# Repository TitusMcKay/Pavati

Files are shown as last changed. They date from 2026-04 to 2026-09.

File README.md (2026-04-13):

so here is some text in the md file idk how to ***write*** md but i should eventualy lol

i learned how to ssh keygen and use that for auth and can now push this new line over ssh
# About
In this repo are files for the battery signal delay box for the Pavati boats
The pcb designs were done in KiCad
The 3d models will be done in FreeCAD

# How To Source Components
To select components for procurment see [procurment.md](./procurment.md)

There is a [bom](https://en.wikipedia.org/wiki/Bill_of_materials) in [battery switch delay.tsv](./battery%20switch%20delay.tsv) that can be used to place manufatuer part numbers on the procurment list 

# How to view
## PCB
To view in the web go [here](https://kicanvas.org/?repo=https%3A%2F%2Fgithub.com%2FTitusMcKay%2FPavati)

To view on your machine clone the repo and open the project in KiCad

## 3D
You can view the case [here](https://3dviewer.net/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).

If you want the best viewing experience open the [design files](./3d) in [FreeCAD](https://github.com/freecad/freecad), or open .step files in your 3d printer slicer or CAD software of choice

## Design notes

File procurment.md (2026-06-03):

# Instructions
Use this list to add parts to an order from a market place like DigiKey or Mouser.

# Electronic Components

## Capacitors

C1
  ```
  KEMET 399-EXV106M025S9BAACT-ND
  ```
  ```
  Panasonic Electronic Components 10-EEE-FN1C100RCT-ND
  ```
  ```
  Panasonic Electronic Components 10-EEE-FN1E100RCT-ND
  ```
C2
  ```
  Murata Electronics GRM21BR61H106KE43L
  ```
  ```
  Samsung Electro-Mechanics CL21A106KBYQNNE
  ```
  ```
  TDK Corporation C2012X5R1H106K125AC
  ```
  
## Diodes

D1
  ```
  Diodes Incorporated MMSZ5231B-7-F
  ```
  ```
  Diodes Incorporated BZT52C4V7-13-F
  ```
  ```
  Panjit International Inc. BZT52-C5V1_R1_00001
  ```

## Relay
K2
  ```
  CIT Relay and Switch 2449-J1071CS12VDC.36-ND
  ```
  ```
  Omron Electronics Inc-EMC Div G6E-134P-US DC12  #  dont use
  ```

## Terminal Block
J1
  ```
  Same Sky (Formerly CUI Devices) 102-6136-ND
  ```
  ```
  Adam Tech 2057-EBBA-04-C-SS-BU-ND
  ```
  ```
  Würth Elektronik 732-10957-ND
  ```
 
## Transistor

Q1
  ```
  MCC (Micro Commercial Components) BC817-40-TPMSCT-ND
  ```
  ```
  onsemi BC846BLT1GOSCT-ND
  ```
  ```
  Nexperia USA Inc. 1727-4312-1-ND
  ```

## Resistors

R1,R2,R3
  ``` 
  Stackpole Electronics Inc RMCF0805JT10K0CT-ND
  ```
  ```
  Stackpole Electronics Inc RMCF0805FT10K0CT-ND
  ```
  ```
  YAGEO 311-10KARCT-ND 
  ```

## Voltage Regulator

U2
  ```
  Microchip Technology MIC2920A-12WS-CT-ND
  ```
<!--  - Texas Instruments 296-46112-1-ND -->

# Mechanical parts

## O-Ring

  McMaster part for 50A Durometer Dash 150 Buna-N Rubber O-Ring:
  ``` 
  2418T357
  ```
## Screws

  McMaster part number for a 1/2" No. 4 stainless steel plastic tapping screw:
  ```
  96001A210 
  ```
  McMaster part number for a 6mm M2 steel plastic tapping screw:
  ```
  96817A209
  ```

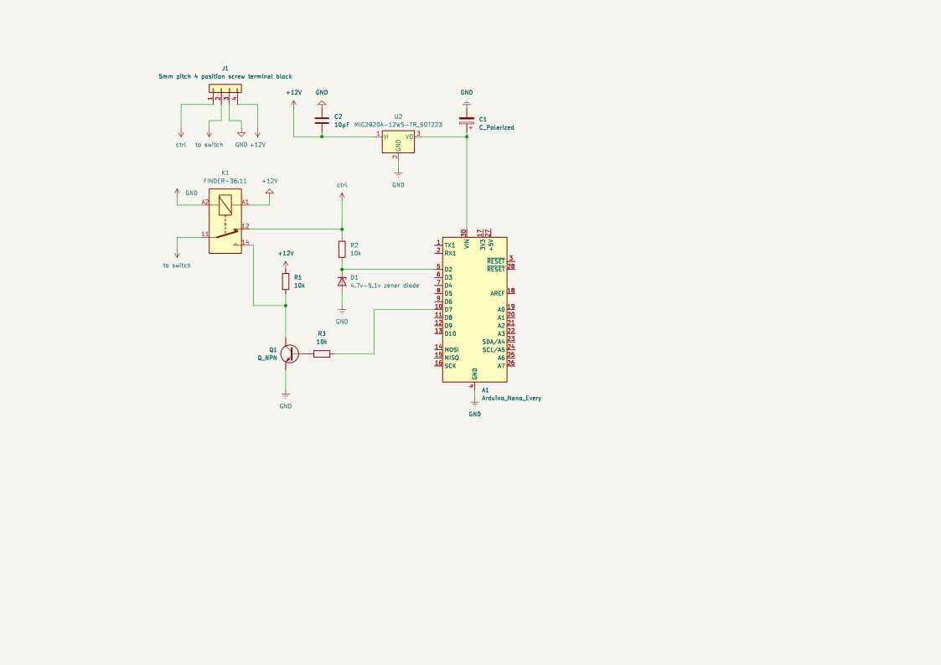
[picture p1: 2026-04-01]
battery switch delay.png

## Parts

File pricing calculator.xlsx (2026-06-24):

component | $/pc | quantity | cost | overhead | cost | units per inconvience | cost
C1 | 0.256 | 1 | 0.256 | digikey shpping | 6.99 | 3 | 2.33
C2 | 0.183 | 1 | 0.183 | digikey tariff | 2.36 | 3 | 0.7866666667
D1 | 0.114 | 1 | 0.114 | oshprak shpping | 8 | 3 | 2.666666667
K2 | 0.701 | 1 | 0.701 |  |  |  | 0
J1 | 0.549 | 1 | 0.549 |  |  |  | 0
Q1 | 0.081 | 1 | 0.081 |  |  |  | 0
R1,R2,R3 | 0.032 | 3 | 0.096 |  |  |  | 0
U1 | 1.49 | 1 | 1.49 |  |  |  | 0
A1 | 5.9 | 1 | 5.9 |  |  |  | 0
header | 0.48 | 2 | 0.96 |  |  |  | 0
pcb | 11.53333333 | 1 | 11.53333333 |  |  |  | 0
case | 1.5 | 1 | 1.5
pcb screw | 0.3564 | 4 | 1.4256
lid screw | 0.2664 | 8 | 2.1312
o-ring | 0.746 | 1 | 0.746
4 strand wire | 2.754 | 1 | 2.754
 |  |  | 0
 |  |  | 0 |  |  | cost of components | overhead | fun profits | round to clean # for price to charge
 |  |  | 0 |  |  | 30.42013333 | 5.783333333 | 72.40693333 | 108.6104
 |  |  | 0
 |  |  | 0
 |  |  | 0
 |  |  | 0
 |  |  | 0
 |  |  | 0

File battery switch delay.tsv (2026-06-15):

Reference | Qty | Value | DNP | Exclude from BOM | Exclude from Board | Footprint | Datasheet | Description
A1 | 1 | Arduino_Nano_Every |  |  |  | Module:Arduino_Nano | https://content.arduino.cc/assets/NANOEveryV3.0_sch.pdf | Arduino Nano Every
C1 | 1 | C_Polarized |  |  |  |  |  | Polarized capacitor
C2 | 1 | 10μF |  |  |  | Capacitor_SMD:C_0805_2012Metric_Pad1.18x1.45mm_HandSolder |  | Unpolarized capacitor, rated for 40v
D1 | 1 | 4.7v-5.1v zener diode |  |  |  | Diode_SMD:D_SOD-123 | http://diotec.com/tl_files/diotec/files/pdf/datasheets/zpd1 | Zener Diode
J1 | 1 | 5mm pitch 4 position screw terminal block |  |  |  | TerminalBlock:TerminalBlock_MaiXu_MX126-5.0-04P_1x04_P5.00mm | https://mm.digikey.com/Volume0/opasdata/d220001/medias/docus/1080/1935187.pdf | Generic connector, single row, 01x04, script generated (kicad-library-utils/schlib/autogen/connector/)
K1 | 1 | FINDER-36.11 |  |  |  | Relay_THT:Relay_SPDT_Finder_36.11 | https://gfinder.findernet.com/public/attachments/36/EN/S36EN.pdf | FINDER 36.11, SPDT relay, 10A
Q1 | 1 | Q_NPN |  |  |  | Package_TO_SOT_SMD:SOT-23 |  | NPN bipolar junction transistor
R1,R2,R3 | 3 | 10k |  |  |  | Resistor_SMD:R_0805_2012Metric_Pad1.20x1.40mm_HandSolder |  | Resistor
U2 | 1 | MIC2920A-12WS-TR_SOT223 |  |  |  | Package_TO_SOT_SMD:SOT-223-3_TabPin2 | https://ww1.microchip.com/downloads/en/DeviceDoc/mic2920.pdf | 700mA Micropower Low drop-out regulator, Fixed Output 5.0V, SOT-223

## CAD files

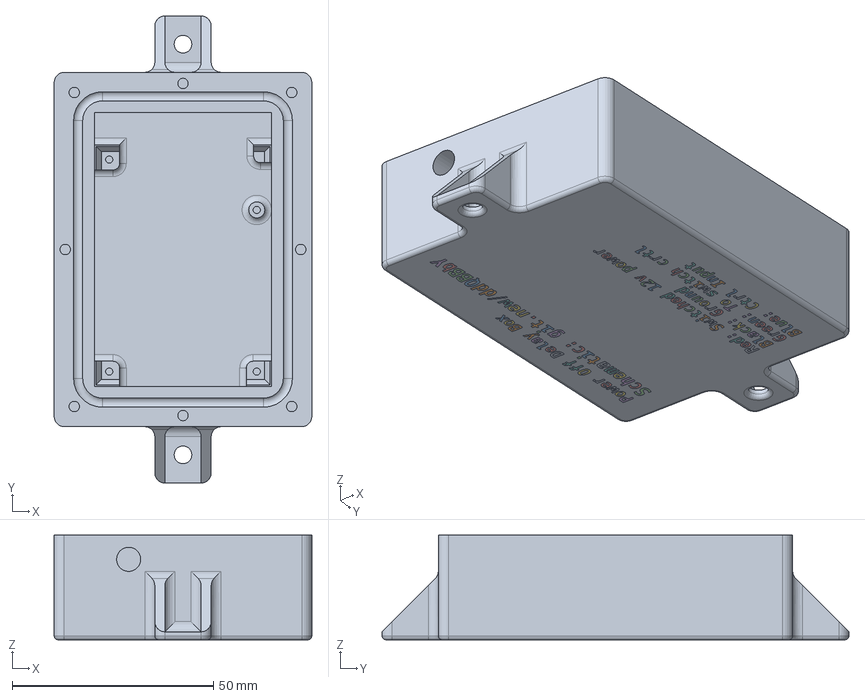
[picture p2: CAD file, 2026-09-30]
3d/case.step
64.0 x 116.0 x 26.0 mm

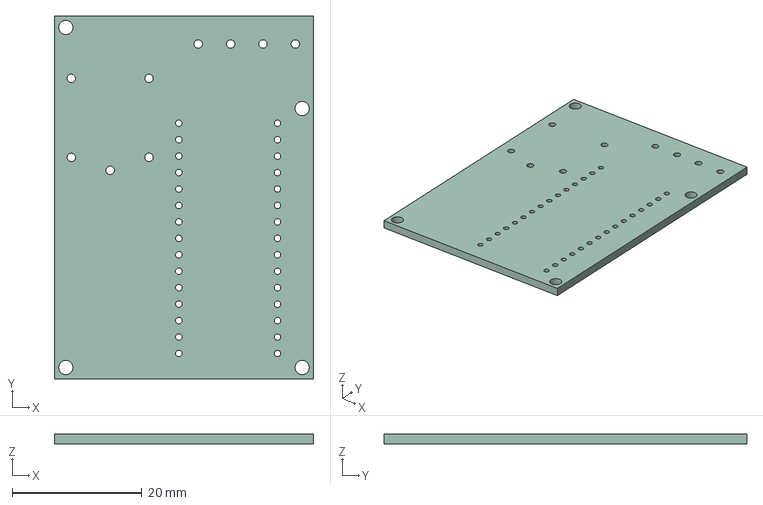
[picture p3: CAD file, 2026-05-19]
battery switch delay.step
40.0 x 56.0 x 1.51 mm

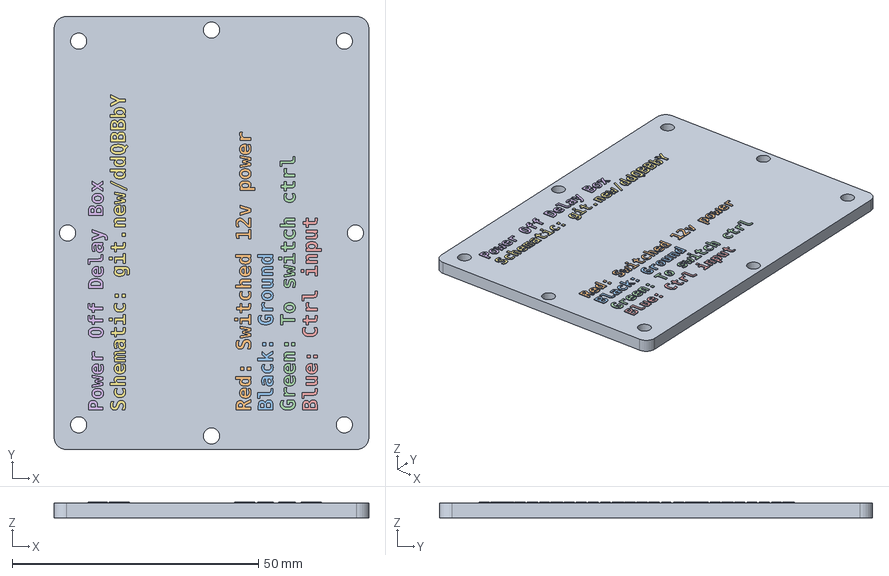
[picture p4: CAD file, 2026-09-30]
3d/lid.FCStd
64.0 x 88.0 x 3.16 mm
red
black
green
blue
description
schematic link

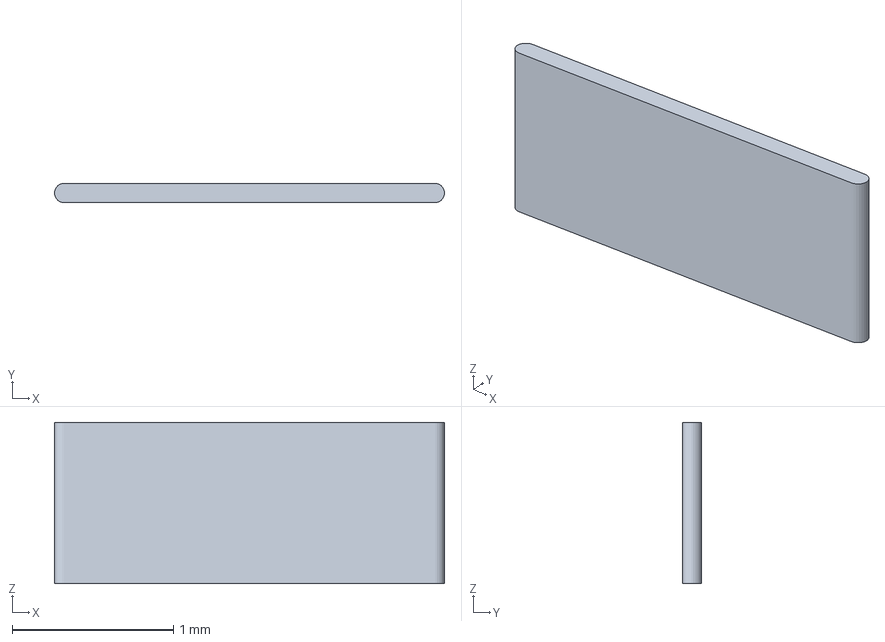
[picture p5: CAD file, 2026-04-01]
ofset.3mf
2.42 x 0.12 x 1.00 mm

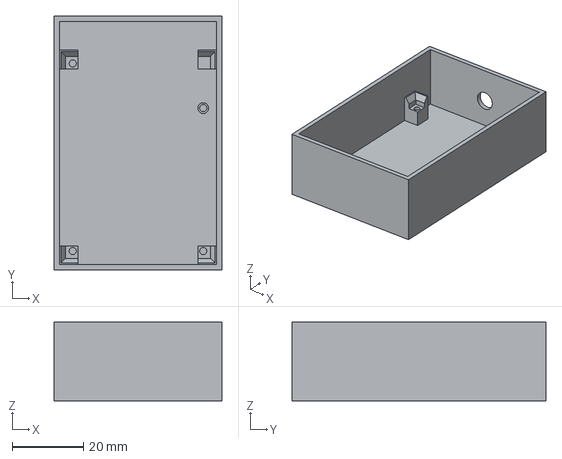
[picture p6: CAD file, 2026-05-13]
3d/case-Body.step
47.0 x 71.0 x 22.0 mm

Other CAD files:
battery switch delay silkscreen.step
3d/case.FCStd
battery switch delay.dxf

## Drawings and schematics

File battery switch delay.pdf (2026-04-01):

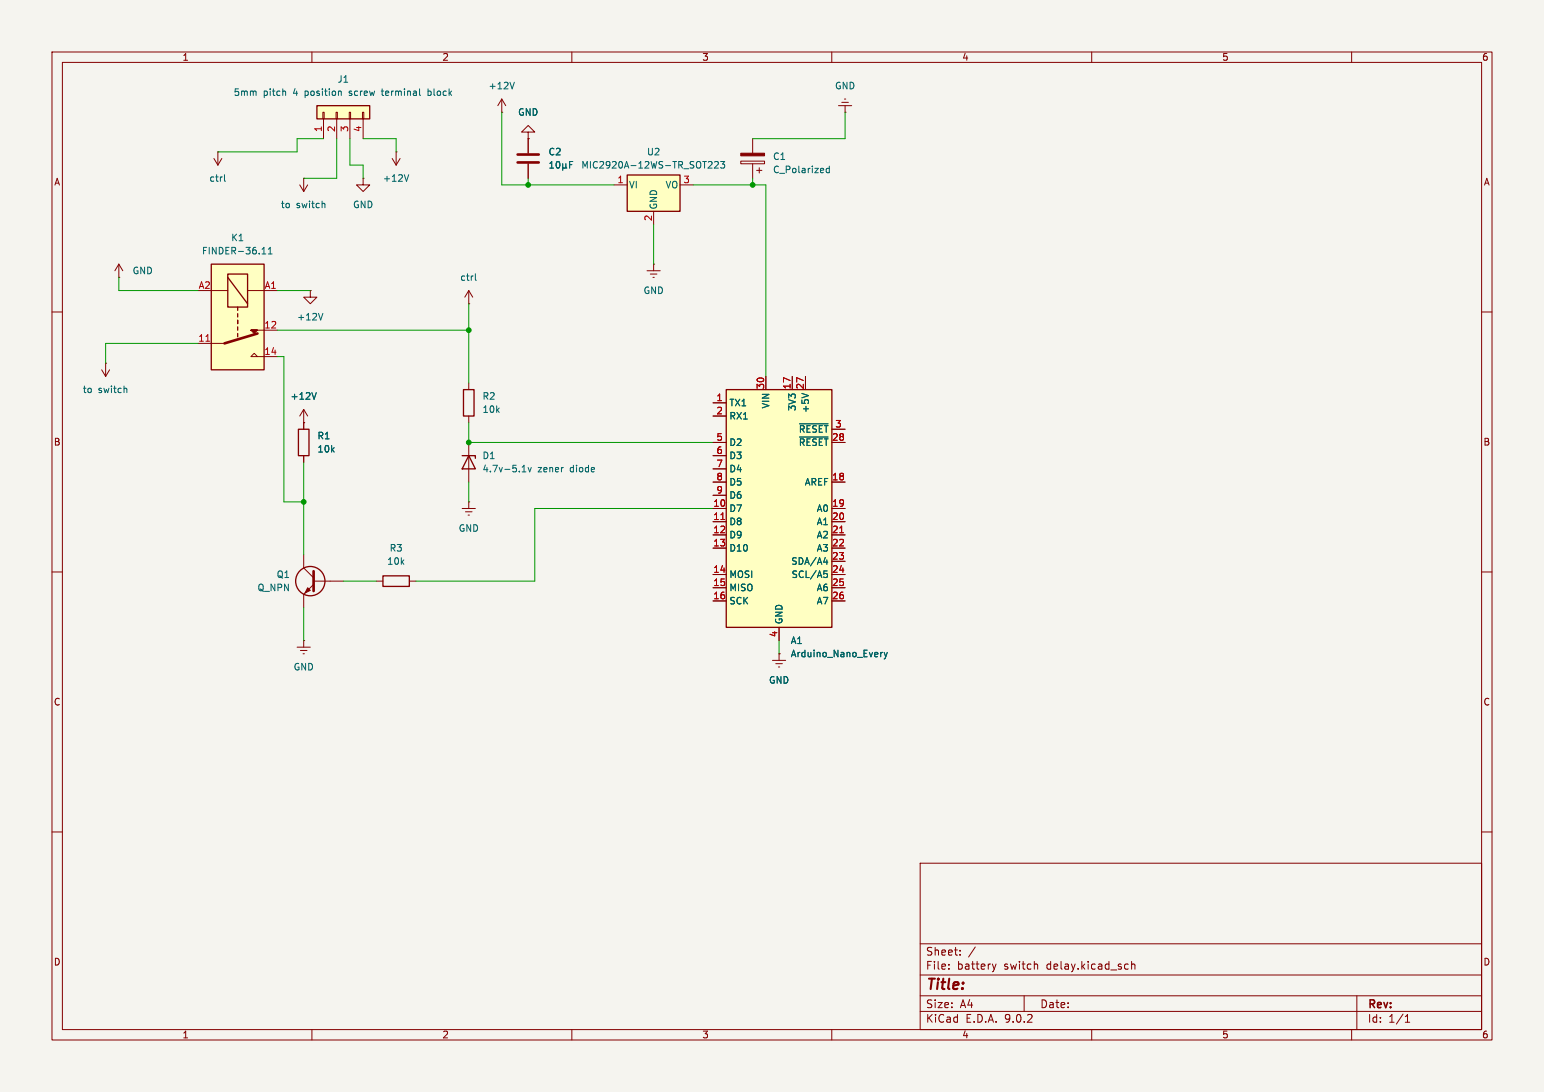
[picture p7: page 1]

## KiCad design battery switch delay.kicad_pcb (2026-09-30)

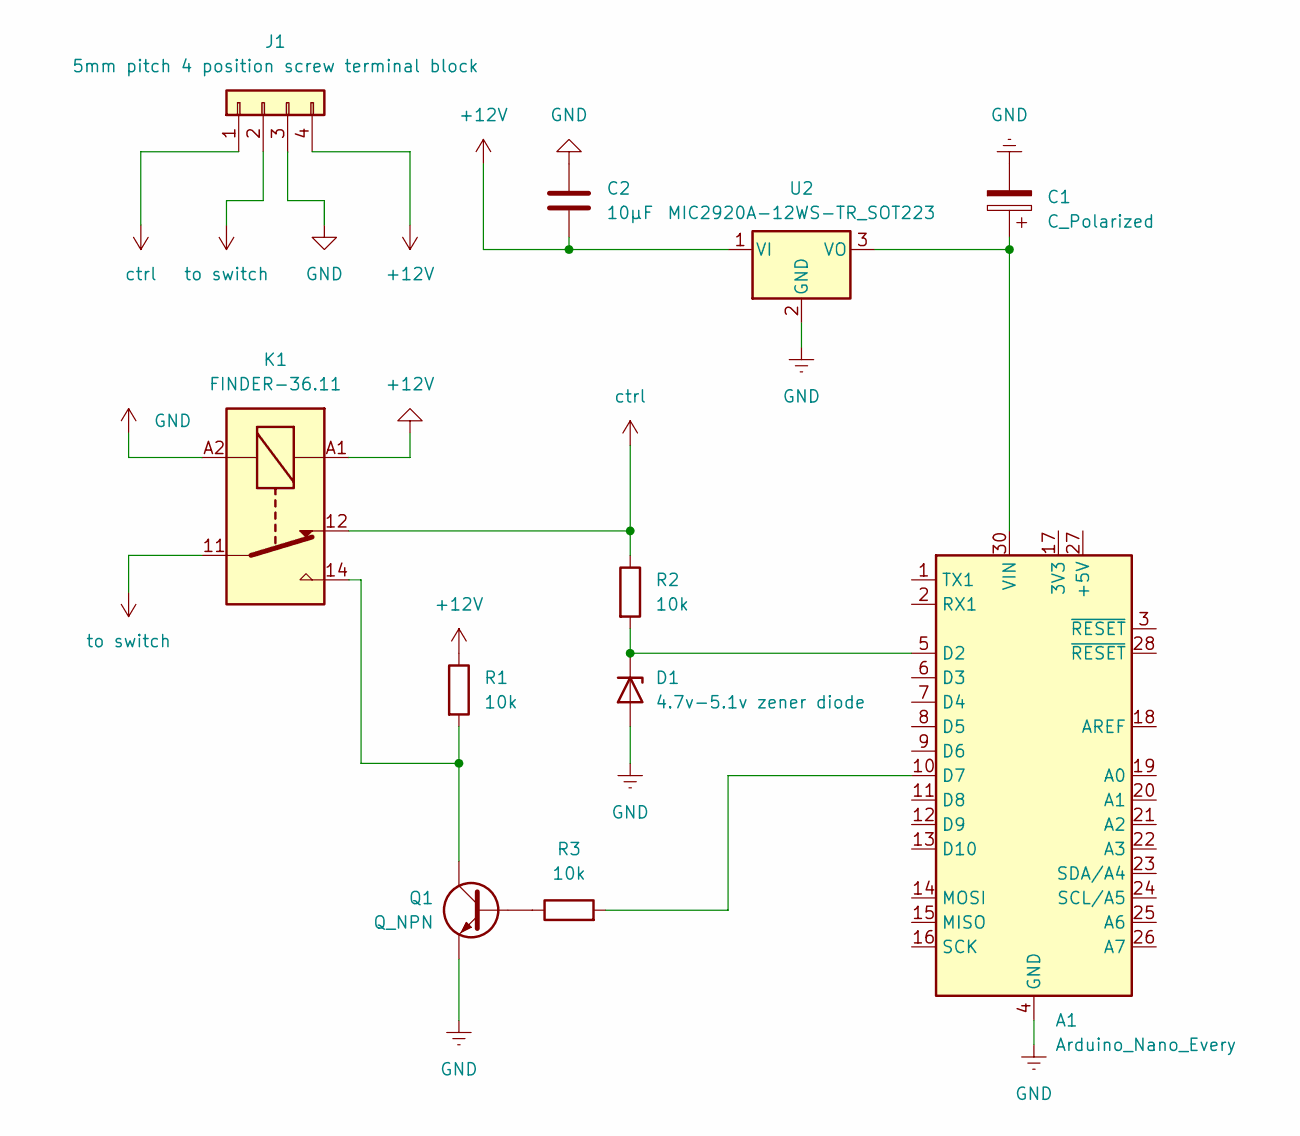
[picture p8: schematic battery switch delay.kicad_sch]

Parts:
A1: Arduino_Nano_Every; Arduino_Nano
C1: C_Polarized
C2: 10μF; C_0805_2012Metric_Pad1.18x1.45mm_HandSolder
D1: 4.7v-5.1v zener diode; D_SOD-123
J1: 5mm pitch 4 position screw terminal block; TerminalBlock_MaiXu_MX126-5.0-04P_1x04_P5.00mm
K1: FINDER-36.11; Relay_SPDT_Finder_36.11
Q1: Q_NPN; SOT-23
R1, R2, R3: 10k; R_0805_2012Metric_Pad1.20x1.40mm_HandSolder
U2: MIC2920A-12WS-TR_SOT223; SOT-223-3_TabPin2

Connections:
+12V: C2.2, J1.4, K1.A1, R1.1, U2.1 (VI)
GND: A1.4 (GND), A1.29 (GND), C1.2, C2.1, D1.2 (A), J1.3, K1.A2, Q1.2 (E), U2.2 (GND)
unnamed: A1.5 (D2), D1.1 (K), R2.2
unnamed: A1.10 (D7), R3.2
unnamed: A1.30 (VIN), C1.1, U2.3 (VO)
unnamed: Q1.1 (B), R3.1
unnamed: K1.14, Q1.3 (C), R1.2
ctrl: J1.1, K1.12, R2.1
to switch: J1.2, K1.11

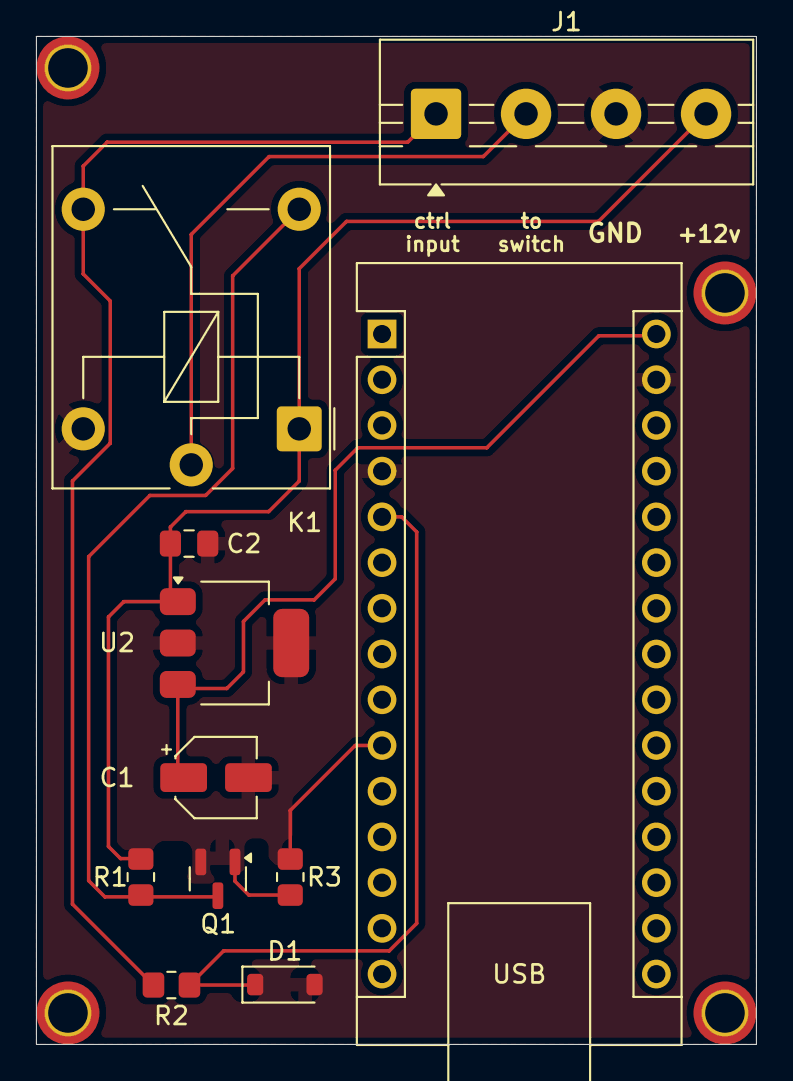
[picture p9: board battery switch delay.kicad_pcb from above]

Board: 2 copper layers, 40.0 x 56.0 mm, 11 parts (0 on the bottom side), 9 nets.

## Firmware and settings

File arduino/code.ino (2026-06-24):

//main pin in is d2
const int fobPin = 2;
const int switchPin = 7;

unsigned long startOfPulse=0;
unsigned long startOfDelay=0;
bool timing = false;
bool offPulse = false;

void setup () {
  pinMode(fobPin, INPUT);
  pinMode(switchPin, OUTPUT);
  digitalWrite(switchPin, HIGH);
  Serial.begin(9600);
}

void loop() {
  Serial.print("\r fobPin bool value:");
  Serial.print( digitalRead(fobPin) );
  Serial.print(" switchPin bool value:");
  Serial.print( digitalRead(switchPin) );
  Serial.print("  time after pulse started:");
  //Serial.print(millis() - startOfPulse);


  if (digitalRead(fobPin) == HIGH){
    if (!timing) { // locks in when pulse started
      startOfPulse = millis();
      timing=true;
    }

    if ((millis() - startOfPulse < 2000) && (millis() - startOfPulse > 250)) {
      offPulse = false;
    }
    if (millis() - startOfPulse > 2000) { // see if you have waited long enough
      startOfDelay = millis();
      offPulse = true;
      //delay(6000); // time before signal is sent out to the switch
      //digitalWrite(switchPin, LOW); // 12v is now common with line going to switch beause of transistor
      //delay(2250); // wait two an a quarter seconds
    }
  } else {
    timing = false;
    //digitalWrite(switchPin, HIGH);
    startOfPulse = millis(); // if ever touches low "timer" resets
    Serial.print(millis() - startOfPulse);
  }
  if (offPulse && (millis() - startOfDelay > 8000)) {
    digitalWrite(switchPin, LOW);
  } else {
    digitalWrite(switchPin, HIGH);
  }
}

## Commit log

2026-03-10 trying multiple lines here gonna add the
    [battery switch delay.tsv]
2026-03-11 added description field to bom
    [battery switch delay.tsv]
2026-03-11 changed the description of caps to include voltage rating
    [battery switch delay.kicad_sch]
2026-03-11 generated bom
    [battery switch delay.tsv]
2026-03-12 added procurment procurment.md and structure inside
    [battery switch delay.kicad_sch]
2026-03-13 added capacitor part numbers to procurment.md
2026-03-13 added zener diodes
2026-03-13 going to bed now
2026-03-15 added resistors and voltage regulator part numbers
2026-03-16 got the transistor the correct footprint hopefully
    [battery switch delay.kicad_pcb, battery switch delay.kicad_sch, battery switch delay.tsv]
2026-03-16 shuffling things around
    [battery switch delay.kicad_pcb]
2026-03-17 did more board layout and actualy have all nets connected. looking at drc so i can be sure
    [battery switch delay.kicad_pcb, battery switch delay.kicad_sch]
2026-03-17 forgor to save lol
    [battery switch delay.kicad_pcb]
2026-03-17 commented out TI voltage regulator from procurement.md
2026-03-17 moved overlaping text in schematic
    [battery switch delay.kicad_sch]
2026-03-17 test commit
    [battery switch delay.kicad_sch]
2026-03-17 moved another thing
    [battery switch delay.kicad_sch]
2026-03-18 changed the cap on the voltage regulator in the schematic and baord
    [battery switch delay.kicad_sch]
2026-03-18 more rand changes ig
    [battery switch delay.kicad_pcb, battery switch delay.kicad_sch]
2026-03-18 moved a trace
    [battery switch delay.kicad_pcb]
2026-03-18 testing kicanvas
    [battery switch delay.kicad_sch]
2026-03-19 changed relay to smth with a much lower price .63 vs /bin/zsh.70 🤯
    [battery switch delay.kicad_pcb, battery switch delay.kicad_sch]
2026-03-19 debuging kicanvas
    [battery switch delay.kicad_pcb]
2026-03-20 probably ready for first order
    [battery switch delay-B_Cu.gbr, battery switch delay-B_Mask.gbr, battery switch delay-B_Paste.gbr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]
2026-03-20 moved text
    [battery switch delay.kicad_pcb]
2026-03-21 zipped up gerbers
2026-03-21 moved some silk screen text
    [battery switch delay.kicad_pcb]
2026-03-28 barely anything
    [battery switch delay.kicad_pcb]
2026-03-30 added qr code and text to the repo
    [battery switch delay.kicad_pcb, battery switch delay.kicad_sch]
2026-03-30 fixed ground pour to include the relay
    [battery switch delay.kicad_pcb]
2026-04-01 did a quick mockup of the case
    [battery switch delay silkscreen.step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]
2026-04-01 added 3d folder
    [battery switch delay.dxf, case.FCStd, ofset.3mf]
2026-04-01 exported case to a step
    [case-Body.step]
2026-04-01 removed .history
    [battery switch delay.kicad_pcb]
2026-04-12 wrote simple code
    [case-Body.step, case.FCStd]
2026-04-27 made code gooder
    [battery switch delay.kicad_pcb, case.FCStd]
2026-05-06 compiles code without errors other than dev setup, tested at pavati but waits for 2 seconds after power on before immedietly setting switch pin to high
    [code.ino]
2026-05-06 reset timer if pin d2 ever touches low
    [battery switch delay.kicad_sch]
2026-05-08 got nowhere but ik that fob and switch pins are low
2026-05-08 verified that timer works by setting timer activation on fob low, after two seconds the switch pin went high. when testing at pavati both fob and switch pins stayed low the entire time. still dont kn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
2026-05-13 made better version of case, still needs lid to be designed. i will have to add a grove for o-ring gasket and screw holes to hold it down. the box still has no way to mounting to a boat so ill have t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
    [case-Body.step, case.FCStd]
2026-05-15 this shi with git should be fixed now
    [case-Body.step, case.FCStd]
2026-05-15 conna push grandfather case again
    [case.FCStd]
2026-05-18 added channel for o-ring. also added screw holes for lid
    [case-Body.step, case.FCStd]
2026-05-18 simple things on case
    [case-Body.step, case.FCStd]
2026-05-19 added screws to procurement.md
    [battery switch delay.step, case-Body.step, case.FCStd]
2026-05-20 added mcmaster oring
    [case.FCStd]
2026-06-03 made channel narrow for better oring seal
    [case-Body.step, case.FCStd]
2026-06-15 added pricing spreadsheet with component costs from digikey. also added arduino from dfrobot and header to procurement.md
    [battery switch delay.tsv, case.FCStd, lid.FCStd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]
2026-06-18 6 second delay before signal is sent
    [pricing calculator.xlsx]
2026-06-22 added wire and pricing info. will meet with Chuck tomorrow to talk about selling or sm idk lol
    [case-Body.step, case.FCStd, lid.FCStd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]
2026-06-24 added the ability to abort poweroff if the user sets fob pin to high for just a little bit, will test on boat tomorrow
    [pricing calculator.xlsx]
2026-06-24 will only abort power off if signal is received and is between .25 and 2 seconds long
2026-06-30 making tag
    [case-Body.step, case.FCStd, lid.FCStd]
